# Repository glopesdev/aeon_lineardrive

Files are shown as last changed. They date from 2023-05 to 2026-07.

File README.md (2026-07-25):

# Aeon LinearDrive

Commutator linear drive Harp device.

Provides control of the linear drive to control the position of the commutator from Bonsai.

## Dependencies

The target must be running a firmware image built from the v1.18-swc branch of the MicroPython project.

Additionally, the SWC microharp package must be present on the filesystem of the target.

## Harp register map

| Register | MessageType | Address | PayloadType | Description |
| --- | --- | --- | --- | --- |
| SetSpeed | Write | 33 | S16 | Set Linear rail velocity, [-7583, 7583] rpm. |
| Speed | Event | 34 | S16 | Current Linear rail velocity, [-7583, 7583] rpm. |
| EnableMotorDriver | Write | 40 | U8 | Linear rail control, 0 = disable, 1 = enable. |
| LimitPosition | Write | 41 | S32 | Linear rail position limits, default -1000, 160000 encoder counts. |
| HomePosition | Write | 42 | S32 | Linear rail home position, in encoder counts. |
| SetPosition | Write | 43 | S32 | Linear rail goto position, in encoder counts. |
| Position | Event | 44 | S32 | Linear rail current position, in encoder counts. |
| LimitSpeed | Write | 45 | U16 | Linear rail speed limit, default 7583 rpm. |
| LimitContinuousCurrent | Write | 46 | U16 | Linear rail Continuous current limit, default 900 mA. |
| LimitPeakCurrent | Write | 47 | U16 | Linear rail Peak current limit, default 900 mA. |
| EnableLimitPosition | Write | 48 | U8 | Position range limit control, 0 = disable, 1 = enable. |

Velocity is the motor shaft speed in rpm and position is in motor encoder counts, both passed to the FAULHABER controller as-is. No gearhead or lead-screw conversion to linear displacement is applied on the device.

## Quick Start

To control the position of the linear drive:
- set home
- enable the drive
- set position

## Citation Policy

If you use this software or hardware, please cite it as below:

D. Campagner, J. Bhagat, G. Lopes, L. Calcaterra, A. G. Pouget, A. Almeida, T. T. Nguyen, C. H. Lo, T. Ryan, B. Cruz, F. J. Carvalho, Z. Li, A. Erskine, J. Rapela, O. Folsz, M. Marin, J. Ahn, S. Nierwetberg, S. C. Lenzi, J. D. S. Reggiani, SGEN group – SWC GCNU Experimental Neuroethology Group. _Aeon: an open-source platform to study the neural basis of ethological behaviours over naturalistic timescales._ Preprint at https://doi.org/10.1101/2025.07.31.664513 (2025)



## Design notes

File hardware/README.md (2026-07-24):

# Aeon Linear Drive

Complete hardware designs for the Linear Drive used in project Aeon.

## Folder Structure

### eCAD

The Altium Project folder contains the original Altium Designer Project while the other folders contain the Documentation, Assembly and Fabrication data.
### mCAD

This folder contains the complete mechanical design in Inventor 2023 project format.

The main assembly for the complete model is **ND.NeuroLink._Main.iam**

## FAULHABER components

The linear drive is built around FAULHABER parts. Their datasheets and manuals are copyright DR. FRITZ FAULHABER GMBH & CO. KG and are not redistributed here. Download the current versions from the FAULHABER website.

### Datasheets

* Brushless DC-servomotor [Series 4490 ... B](https://www.faulhaber.com/en/products/series/4490b/)
* Planetary gearhead [Series 42GPT](https://www.faulhaber.com/en/products/series/42gpt/)

### Manuals

* Technical Manual for the MCBL/MCDC/MCLM 3002/03/06 motion controllers, document 7000.05038
* Communication and Function Manual for the MCBL/MCDC 300x RS controllers over RS232, document 7000.05029

Both manuals are in the Downloads section of the controller product page at [faulhaber.com](https://www.faulhaber.com), listed under their document numbers.

### Software

The drive is configured with [FAULHABER Motion Manager](https://www.faulhaber.com/en/support/faulhaber-motion-manager/), set up here with version 6.9.1. The configuration for this project is in the `Faulhaber Software` folder, ready to open in Motion Manager. `Linear Drive for Commutator.mpr` is the project and `Param_Linear_Drive.mcp` is the exported motor parameter set.

## Notes

The required software for the project is as follows
* eCAD - Altium Designer 23.5 or newer. Academic licenses can be obtained by contacting [Altium Education](https://www.altium.com/education/)
* mCAD - Inventor Pro 2023 or newer. Academic licenses can be obtained by contacting [Autodesk Education](https://www.autodesk.com/education/home)

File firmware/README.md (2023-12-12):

# Aeon Linear Drive
## Firmware
This folder contains the 4 .py files that constitute the code running on the Pi Pico
### bin Folder
This folder contains the SWC Micropython MicroHarp binary file in uf2 format.

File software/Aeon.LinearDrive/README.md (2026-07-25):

## About

`Aeon.LinearDrive` provides an asynchronous API and reactive operators for data acquisition and control of Aeon LinearDrive devices.

## How to Use

To use `Aeon.LinearDrive` for visual reactive programming, please install this package using the [Bonsai package manager](https://bonsai-rx.org/docs/articles/packages.html).

The package can also be used from any .NET application:
```c#
using Aeon.LinearDrive;

using var device = await Device.CreateAsync("COM3");
var whoAmI = await device.ReadWhoAmIAsync();
var deviceName = await device.ReadDeviceNameAsync();
var timestamp = await device.ReadTimestampSecondsAsync();
Console.WriteLine($"{deviceName} WhoAmI: {whoAmI} Timestamp (s): {timestamp}");
```

## Feedback & Contributing

`Aeon.LinearDrive` is released as open-source under the [BSD 3-Clause license](https://licenses.nuget.org/BSD-3-Clause). Bug reports and contributions are welcome at [the GitHub repository](https://github.com/SainsburyWellcomeCentre/aeon_lineardrive).

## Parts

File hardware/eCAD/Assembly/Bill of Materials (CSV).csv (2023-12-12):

Comment | Description | Designator | Quantity
C0603-100nF-100V-10%-X7R | 0.1µF ±10% 100V Ceramic Capacitor X7R 0603 (1608 Metric) | C1, C4, C9, C10, C11, C12, C13 | 7
C0603-1uF-25V-10%-X7R | 1µF ±10% 25V Ceramic Capacitor X7R 0603 (1608 Metric) | C2, C3, C5, C7 | 4
C0805-4.7uF-16V-5%-X7R | 4.7uF ±5% 16V Ceramic Capacitor X7R 0805 (2012 Metric) | C6, C8 | 2
SSW-120-01-x-S | Conn Socket Strip SKT 20 POS 2.54mm Solder ST Thru-Hole | J1 | 1
SSW-120-01-x-S - 21-40 | Conn Socket Strip SKT 20 POS 2.54mm Solder ST Thru-Hole (pins 21 - 40) | J2 | 1
SJ-3566AN | 3.5 mm, Stereo, Right Angle, Through Hole, SPDT Switch, Audio Jack Connector | J3 | 1
853-004-213R001 | CONN PLUG FMALE 4POS GOLD SOLDER | J4 | 1
RJULE4218201 | Modular Jack - Right Angle, Input Output Connectors RJ45, 8P8C, Without LEDs, Shield. | J5, J6 | 2
156125RS57000 | Single Color LED | LED1 | 1
R0603-1k5-1/16W-0.1% | Surface Mount Resistor 1k5 Ohm 1/16 W 0.1% 0603 (1608 Metric) | R1 | 1
R0603-10R-1/16W-0.1% | Surface Mount Resistor 10 Ohm 1/16 W 0.1% 0603 (1608 Metric) | R2 | 1
R0603-10k-1/16W-0.1% | Surface Mount Resistor 10k Ohm 1/16 W 0.1% 0603 (1608 Metric) | R3, R4, R9, R10, R14, R15 | 6
R0603-1k-1/16W-0.1% | Surface Mount Resistor 1k Ohm 1/16 W 0.1% 0603 (1608 Metric) | R5 | 1
R0603-100k-1/16W-0.1% | Surface Mount Resistor 100k Ohm 1/16 W 0.1% 0603 (1608 Metric) | R6 | 1
R0603-150R-1/16W-0.1% | Surface Mount Resistor 150 Ohm 1/16 W 0.1% 0603 (1608 Metric) | R7, R8 | 2
R0603-620R-1/16W-0.1% | Surface Mount Resistor 620 Ohm 1/16 W 0.1% 0603 (1608 Metric) | R11, R12, R16, R17 | 4
R0603-110R-1/16W-0.1% | Surface Mount Resistor 110 Ohm 1/16 W 0.1% 0603 (1608 Metric) | R13, R18 | 2
PTS645VM83-2LFS | Switch Tactile N.O. SPST Round Button PC Pins 0.05A 12VDC 100000Cycles 1.57N Bracket Mount/Through Hole Bulk | S1 | 1
Solder Bridge 0603 On | Solder Bridge 0603 ON | SB3, SB5, SB8, SB10, SB11, SB12 | 6
AP2112K-3.3TRG1 | Fixed Positive LDO Regulator, 3.3V, 0.4V Dropout, CMOS, PDSO5 | U1 | 1
TPD3E001DRLR | Low-Capacitance 3-Channel +/-15KV ESD-Protection Array for High-Speed Data Interfaces 5-SOT-5X3 | U2 | 1
LTC4332HUFD#PBF | SPI Extender Over Rugged Differential Link | U3, U4 | 2
SN75C3221PWR | IC RS232 DRVR/RCVR 1-CH 16-TSSOP | U5 | 1

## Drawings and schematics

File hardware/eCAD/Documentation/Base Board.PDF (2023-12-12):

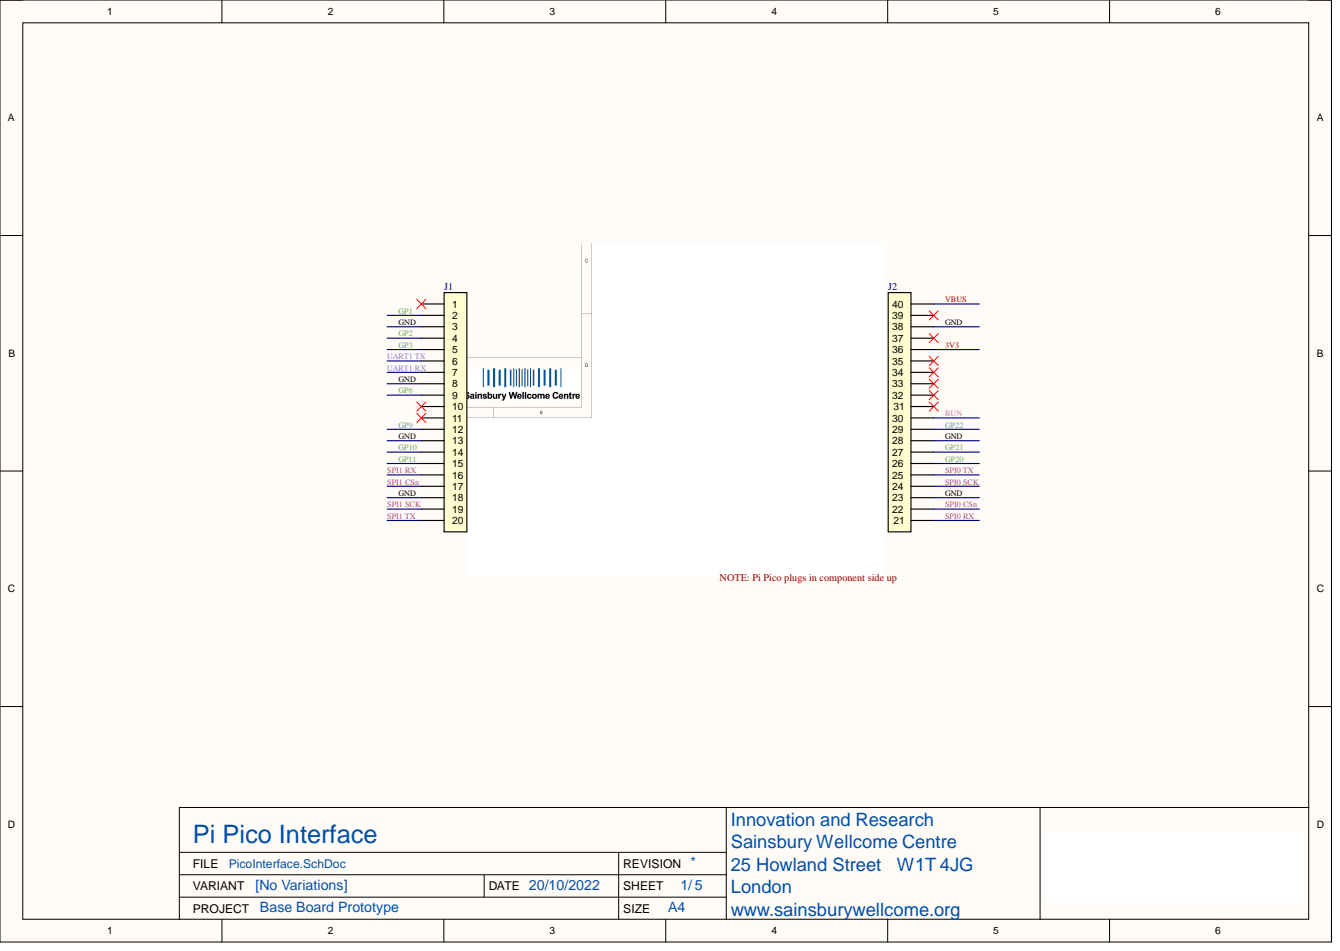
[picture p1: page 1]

GND GND

NOTE: Pi Pico plugs in component side up

Pi Pico Interface | Innovation and Research Sainsbury Wellcome Centre 25 Howland Street W1T 4JG London w w w.sainsbury wellcome.or g

FILE PicoInterface.SchDoc | * REVISION

PROJECT Base Board Prototype VARIANT [No Variations]

DATE 20/10/2022 | SHEET 1 / 5

SIZE A4

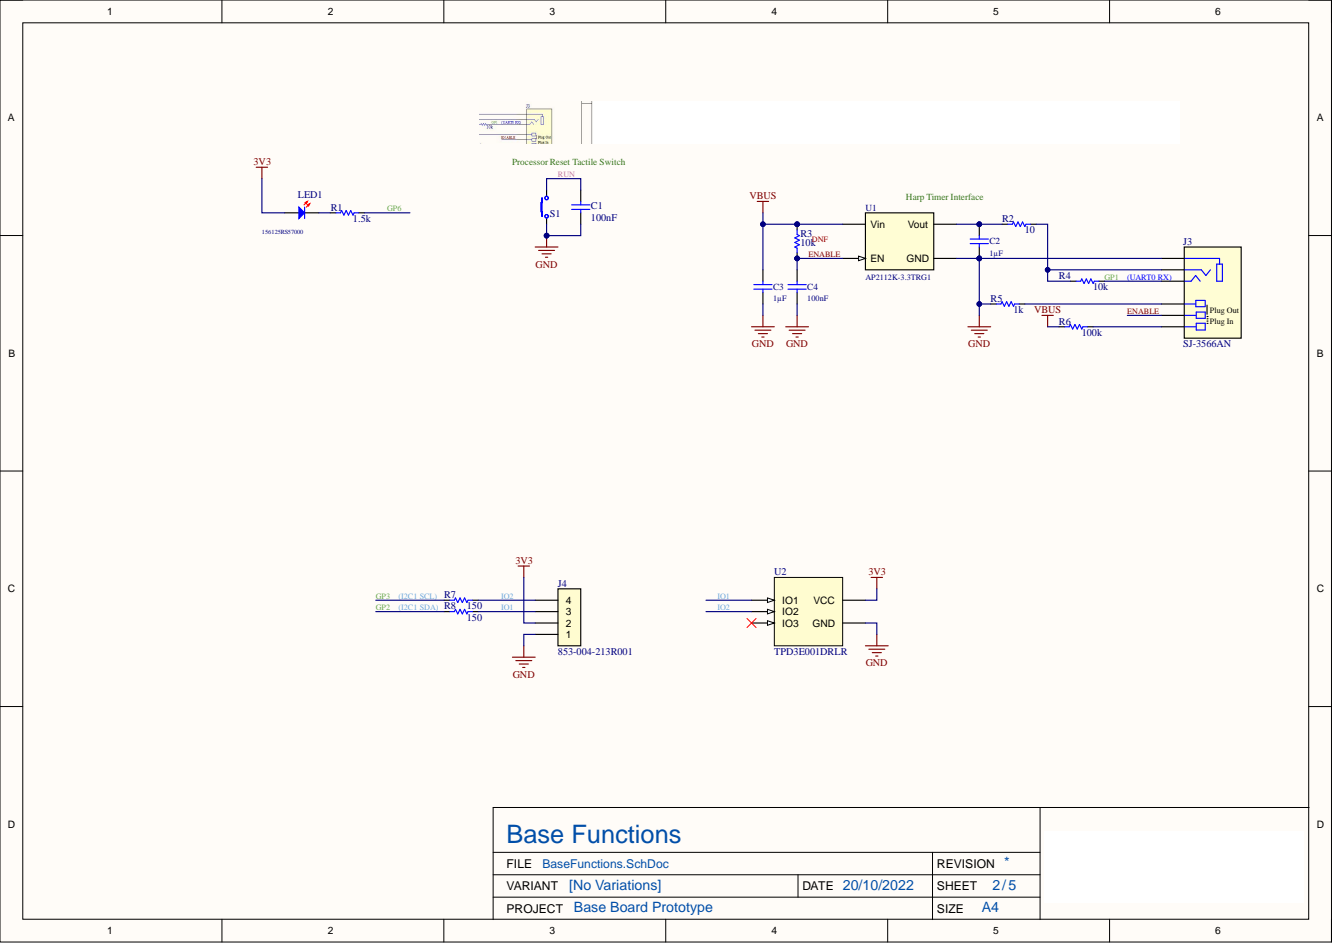
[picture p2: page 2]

Processor Reset Tactile Switch

Base Functions

FILE BaseFunctions.SchDoc | * REVISION
VARIANT [No Variations] | DATE 20/10/2022 | SHEET 2 5 /

PROJECT Base Board Prototype | | SIZE A4

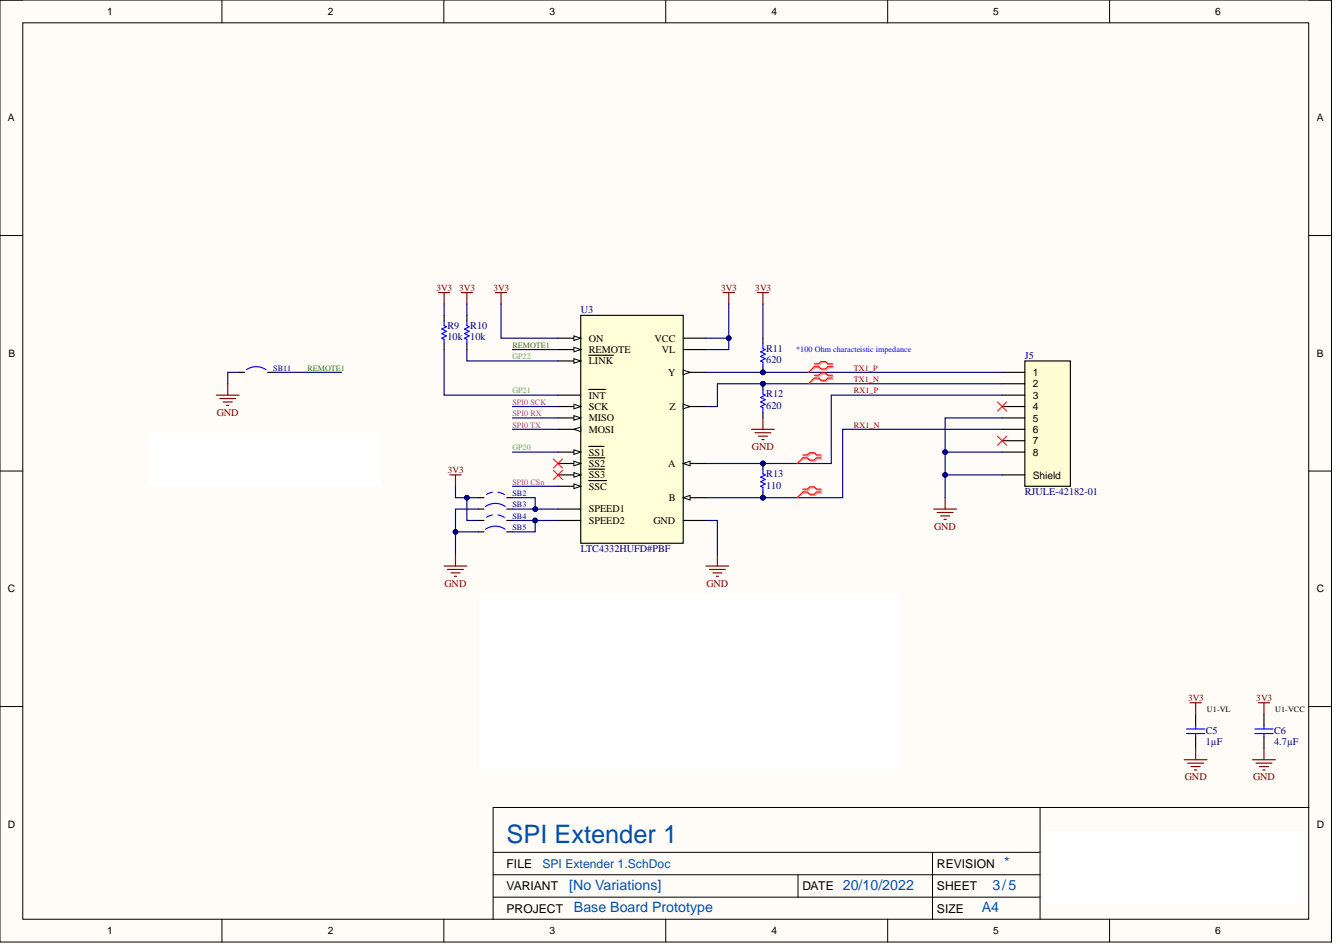
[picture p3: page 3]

GND

SPI Extender 1

FILE SPI Extender 1.SchDoc | * REVISION

PROJECT Base Board Prototype VARIANT [No Variations]

DATE 20/10/2022 | SHEET 3 / 5

SIZE A4

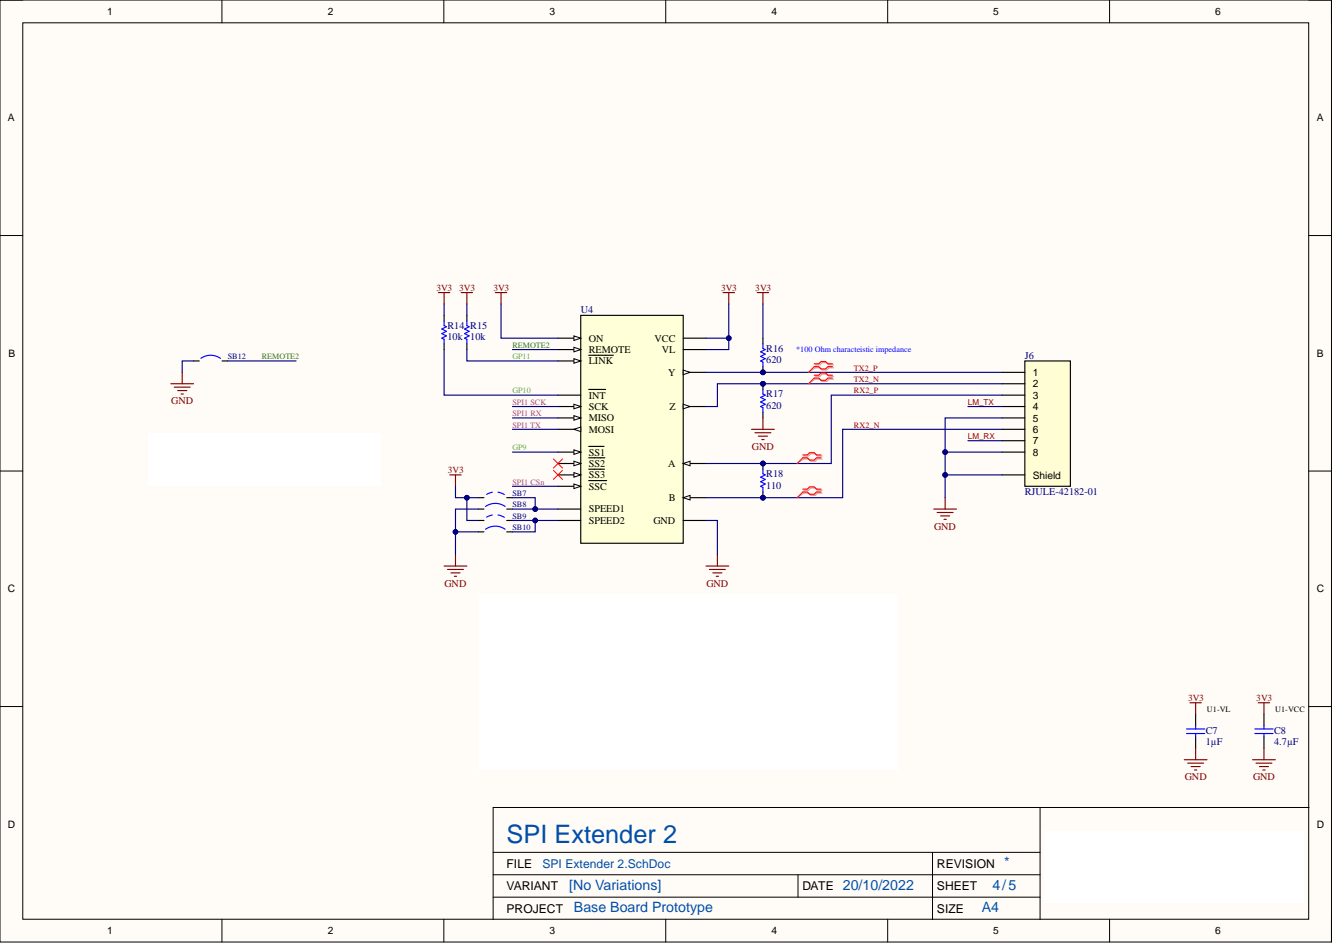
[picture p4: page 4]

SPI Extender 2

FILE SPI Extender 2.SchDoc | * REVISION

PROJECT Base Board Prototype VARIANT [No Variations]

DATE 20/10/2022 | SHEET 4 / 5

SIZE A4

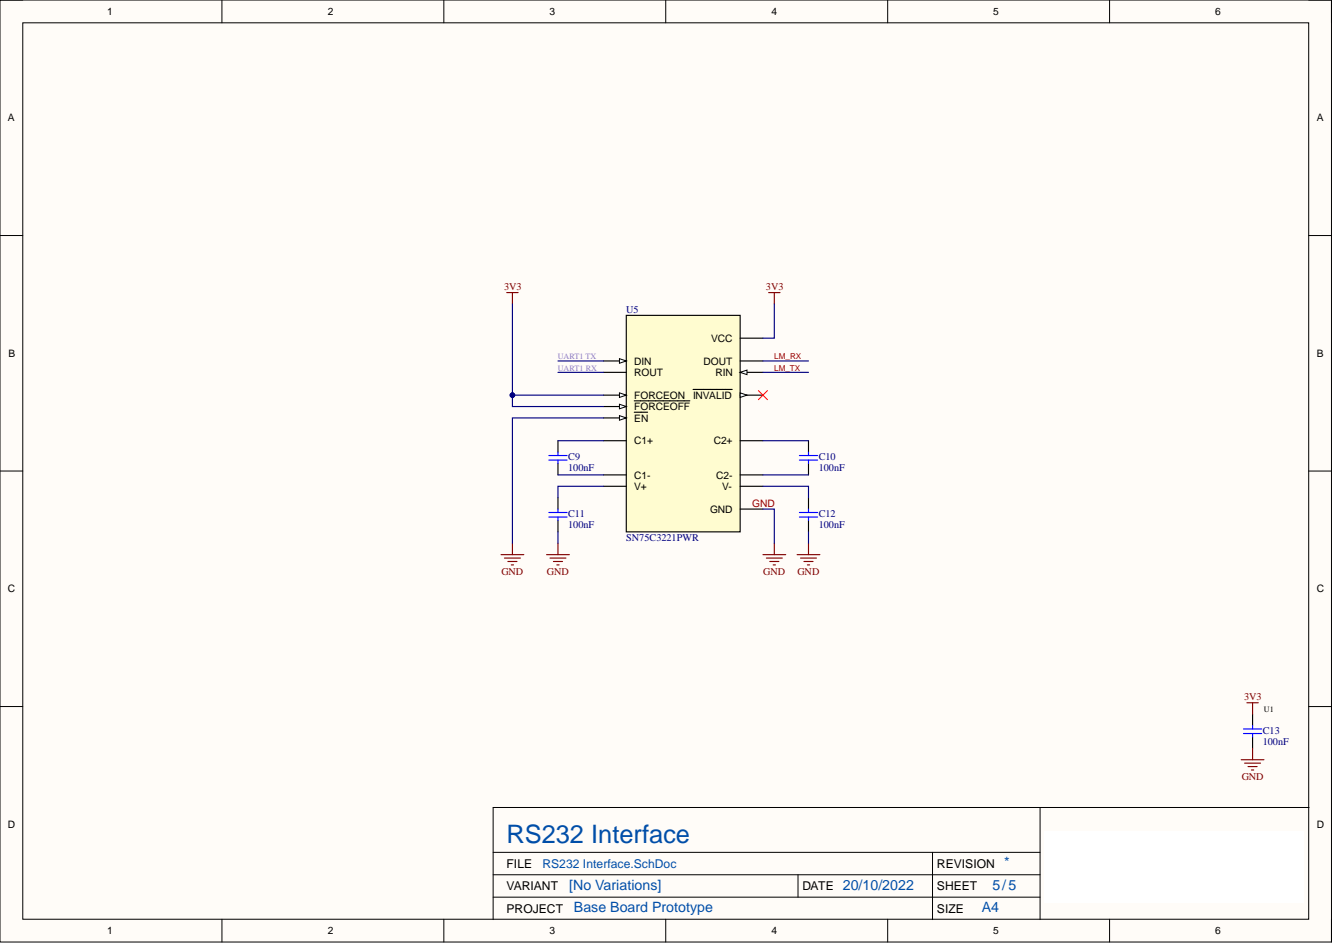
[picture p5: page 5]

RS232 Interface

FILE RS232 Interface.SchDoc | * REVISION

PROJECT Base Board Prototype VARIANT [No Variations]

DATE 20/10/2022 | SHEET 5 / 5

SIZE A4

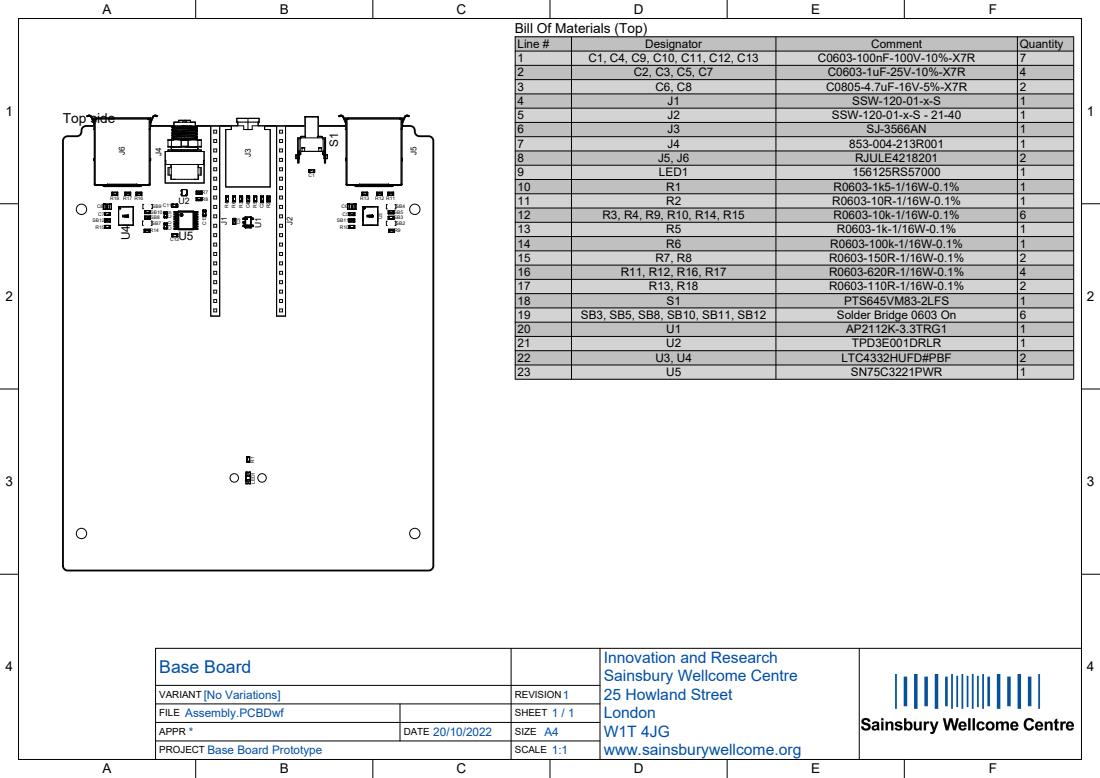
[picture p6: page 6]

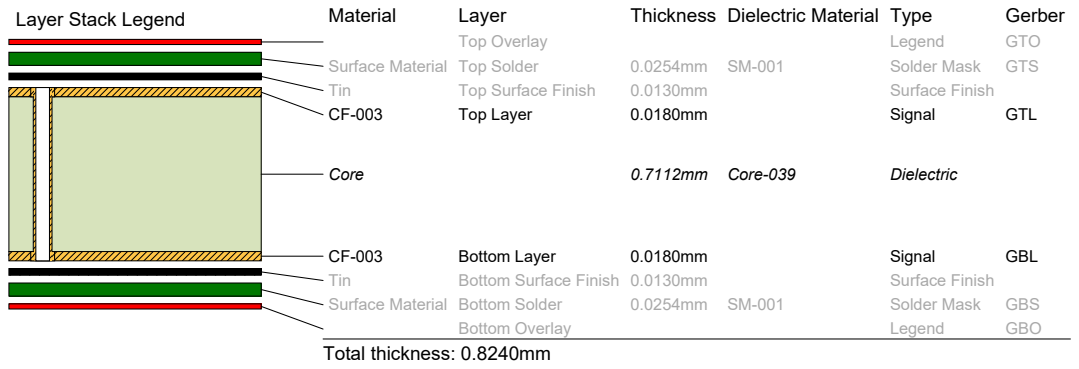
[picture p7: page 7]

[No Variations] VARIANT | 1 REVISION
FILE Fabrication.PCBDwf | | SHEET 1 / 2
APPR * | DATE 20/10/2022 | SIZE A4

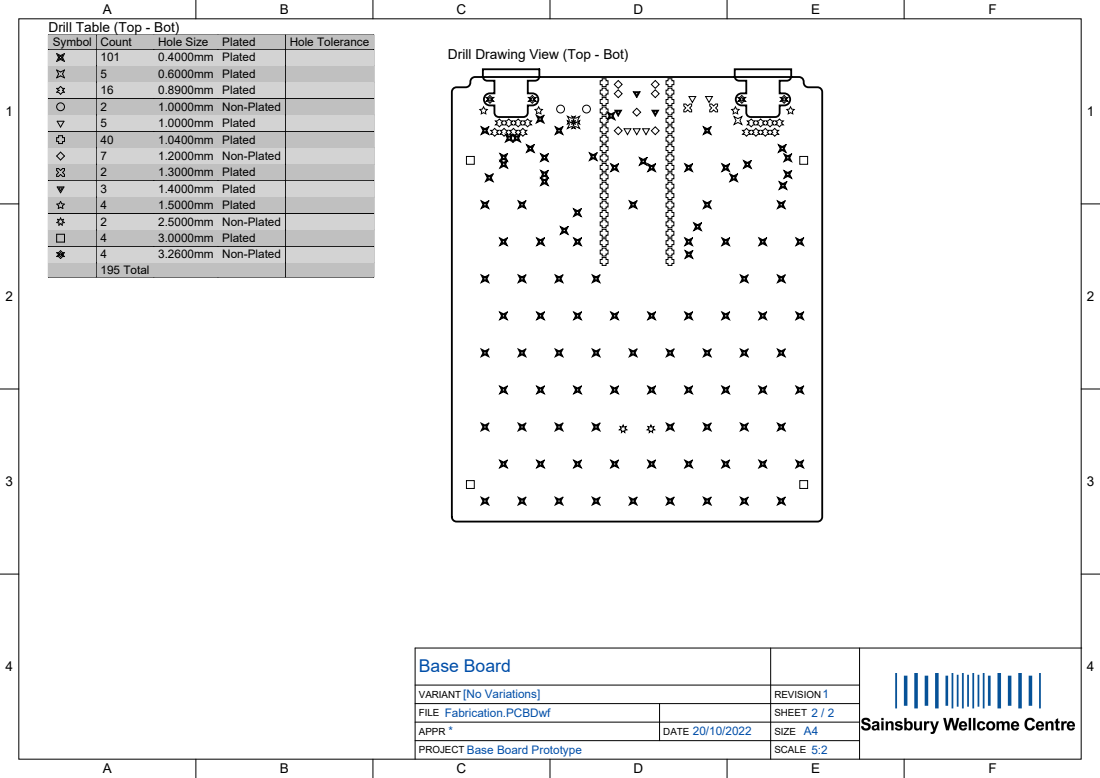
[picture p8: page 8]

Drill Table (Top - Bot)

Symbol | Count | Hole Size | Plated | Hole Tolerance

Drill Drawing View (Top - Bot)

101 | 0.4000mm | Plated
5 | 0.6000mm | Plated
16 | 0.8900mm | Plated
2 | 1.0000mm | Non-Plated
5 | 1.0000mm | Plated
40 | 1.0400mm | Plated
7 | 1.2000mm | Non-Plated
2 | 1.3000mm | Plated
3 | 1.4000mm | Plated
4 | 1.5000mm | Plated
2 | 2.5000mm | Non-Plated
4 | 3.0000mm | Plated
4 | 3.2600mm | Non-Plated
195 Total

[No Variations] VARIANT | 1 REVISION
FILE Fabrication.PCBDwf | | SHEET 2 / 2
APPR * | DATE 20/10/2022 | SIZE A4


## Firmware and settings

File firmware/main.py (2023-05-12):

"""Con Linear Drive main application entrypoint."""
# Import standard library modules.
import uasyncio
from machine import Pin, UART

# Import SWC-IRFL library modules.
import usbcdc
import harpsync
from ptdevice import PtDevice

# Instance the hardware interfaces.
stream = usbcdc.usbcdc(1)
sync = harpsync.harpsync(0)
led = Pin(6, Pin.OUT)
uart = UART(1, 115200, tx=Pin(4), rx=Pin(5, pull=Pin.PULL_UP), timeout=5)
#estop = Pin(2, mode=Pin.IN, pull=Pin.PULL_UP)

# Instance the device object and launch its application.
#theDevice = PtDevice(stream, sync, led, uart, estop)
theDevice = PtDevice(stream, sync, led, uart)
uasyncio.run(theDevice.main())

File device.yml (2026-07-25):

%YAML 1.1
---
# yaml-language-server: $schema=https://raw.githubusercontent.com/harp-tech/reflex-generator/main/schema/device.json
device: LinearDrive
whoAmI: 0000
firmwareVersion: "0.1"
hardwareTargets: "0.0"
registers:
  EnableMotorDriver:
    address: 40
    access: Write
    type: U8
    maskType: EnableFlag
    description: Enables the motor driver.
  LimitPosition:
    address: 41
    access: Write
    type: S32
    length: 2
    description: Configures the position limits of the motor, in encoder counts.
    payloadSpec:
      Minimum:
        offset: 0
        defaultValue: -1000
        description: The minimum allowed position of the motor, in encoder counts
      Maximum:
        offset: 1
        defaultValue: 160000
        description: The maximum allowed position of the motor, in encoder counts
  HomePosition:
    address: 42
    access: Write
    type: S32
    description: Sets the home position of the motor, in encoder counts.
  SetPosition:
    address: 43
    access: Write
    type: S32
    description: Sets the current position of the motor, in encoder counts. Reads return the last instruction.
  Position:
    address: 44
    access: Event
    type: S32
    description: Returns a periodic event with the current position of the motor, in encoder counts.
  LimitSpeed:
    address: 45
    access: Write
    type: U16
    defaultValue: 7583
    description: Sets the maximum speed of the motor, in rpm.
  SetSpeed:
    address: 33
    access: Write
    type: S16
    description: Sets the current speed of the motor, in rpm.
  Speed:
    address: 34
    access: Event
    type: S16
    description: Returns a periodic event with the current speed of the motor, in rpm.
  LimitContinuousCurrent:
    address: 46
    access: Write
    type: U16
    defaultValue: 900
    description: Sets the maximum continuous current limit the drive is able to supply, in mA.
  LimitPeakCurrent:
    address: 47
    access: Write
    type: U16
    defaultValue: 900
    description: Sets the maximum peak current limit the drive is able to supply, in mA.
  EnableLimitPosition:
    address: 48
    access: Write
    type: U8
    maskType: EnableFlag
    description: Enables the position limit.

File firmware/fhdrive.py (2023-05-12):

"""Faulhaber drive class."""
import re


class FaulhaberDrive():
    """Faulhaber drive class."""

    @property
    def en(self):
        return self._en

    @en.setter
    def en(self, value):
        self._en = value
        self._command('EN' if self._en else 'DI')

    @property
    def home(self):
        return self._query('POS')

    @home.setter
    def home(self, value):
        self._parameter('HO', value)

    @property
    def position(self):
        return self._query('POS')

    @position.setter
    def position(self, value):
        self._parameter('LA', value)
        self._command('M')

    @property
    def poslimit(self):
        return self._query('GPL')

    @poslimit.setter
    def poslimit(self, value):
        self._parameter('LL', value)

    @property
    def neglimit(self):
        return self._query('GNL')

    @neglimit.setter
    def neglimit(self, value):
        self._parameter('LL', value)

    @property
    def velocity(self):
        return self._query('GN')

    @velocity.setter
    def velocity(self, value):
        self._parameter('V', value)

    @property
    def speed(self):
        return self._query('GSP')

    @speed.setter
    def speed(self, value):
        self._parameter('SP', value)

    @property
    def cont_cur(self):
        return self._query('GCC')

    @cont_cur.setter
    def cont_cur(self, value):
        self._parameter('LCC', value)

    @property
    def peak_cur(self):
        return self._query('GPC')

    @peak_cur.setter
    def peak_cur(self, value):
        self._parameter('LCP', value)

    @property
    def range_lim(self):
        return '0'

    @range_lim.setter
    def range_lim(self, value):
        self._parameter('APL', value)

    def __init__(self, uart, address):
        """Constructor. Initialises the class."""
        self.uart = uart
        self.address = address
        self.regex = re.compile(b'-?\d+')

    def _command(self, command):
        """Send a command."""
        self.uart.write(f'{self.address}{command}\r')

    def _parameter(self, parameter, value):
        """Set parameter to value."""
        self.uart.write(f'{self.address}{parameter}{value}\r')

    def _query(self, query):
        """Send query and return the parameter value fron the response."""
        self.uart.write(f'{self.address}{query}\r')
        response = self.uart.readline()
        if response is not None:
            match = self.regex.search(response)
            response = int(match.group(0)) if match is not None else None
        return response

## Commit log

2023-05-10 Add first draft of device schema
2023-05-10 Add Device classes
2023-05-10 Fix registers in schema and regenerate Device classes
    [device.yml]
2023-05-10 Fixed bugs for Range limit control and Harp protocol std.
    [ptdevice.py, ptregisters.py]
2023-05-12 update workflow with calibration logic
2023-12-12 Added hardware files and micropython microharp firmware
    [Base Board.PrjPcb, BaseFunctions.SchDoc, Bill of Materials (CSV).csv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]
2023-12-12 added readme and fixed file locations
    [Base Board.PrjPcb, BaseFunctions.SchDoc, Bill of Materials (CSV).csv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]
